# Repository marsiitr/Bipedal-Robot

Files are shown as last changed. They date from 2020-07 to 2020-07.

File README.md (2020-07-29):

# Bipedal-Robot
Srishti 2020

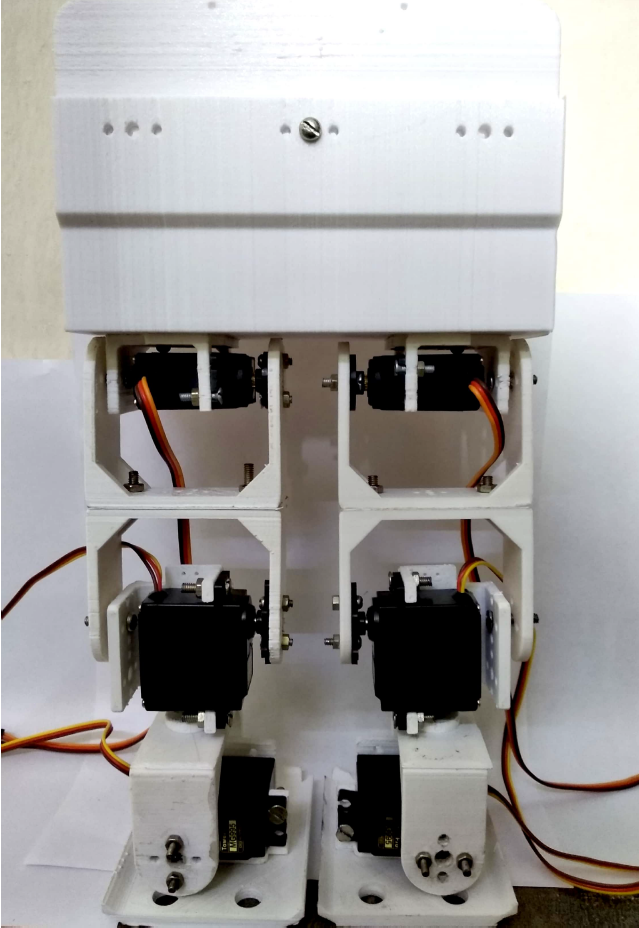
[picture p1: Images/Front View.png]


# Abstract
<div align="justify">The Bipedal Robot is a humanoid robot modeled to mimic the walking of a human, the Robot is designed to have 6 degrees of freedom in total, implying 3 degrees of freedom in each leg, 2 of which are used for moving the leg in forward or backward direction using Servo motors at each joint(hip and knee), while the other degree of freedom is used for balancing the robot using another servo motor when standing on one leg, the mechanical model is designed to avoid extra weight so that the balance of the robot is more stable. The robot is actuated by using the microcontroller Arduino.</div>

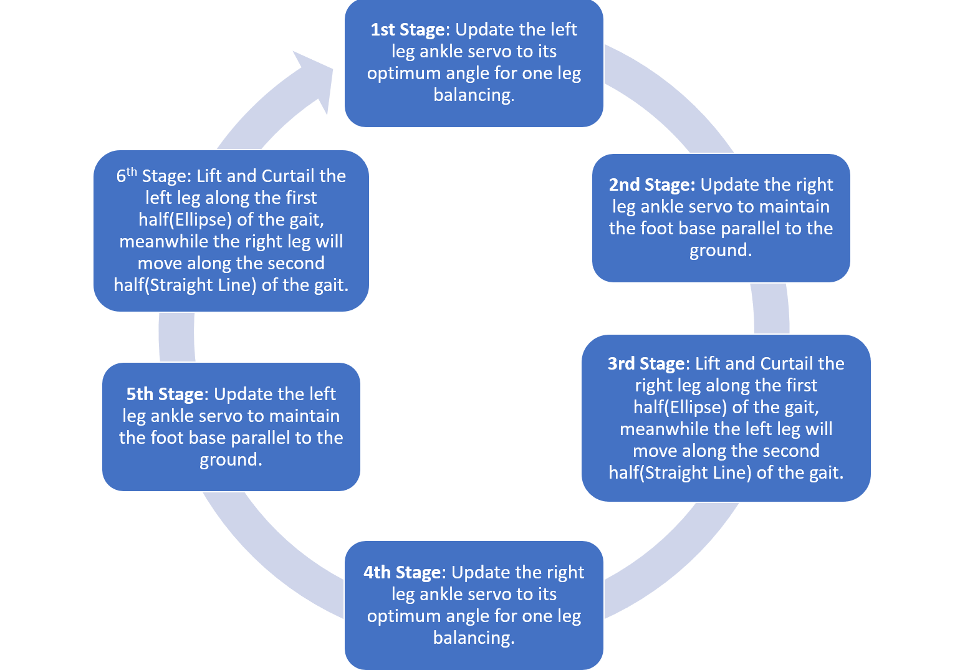
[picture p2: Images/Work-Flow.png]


## Motivation
<div align="justify">Bipedal robots are able to move in areas that are normally inaccessible to wheeled robots, such as stairs and areas littered with obstacles that make wheeled locomotion impossible, also they can be an asset which can work in hazardous conditions.</div>

## Mechanical Aspect

1. <div align="justify">Robot’s size selection - 
   Robot size plays a major role. Based on the cost of project, materials required for fabrication and the no. of actuators can be determined. In this project the size of the robot is preferred so a height of 300mm is decided which includes mountings of the control circuits, but the actual size of the robot is 230mm without controlling circuits.</div>

2. <div align="justify">Degrees of Freedom (D.O.F) - 
   Human leg has got 6 degrees of freedom (Hip – 3 D.O.F , Knee – 1 D.O.F , Ankle – 2 D.O.F) , but implementing all the 6 D.O.F is difficult due to increase in cost of project and controlling of the actuators which become complex, so in this project reduced degrees of freedom is aimed so 3 D.O.F(Ankle , Knee and Hip) per leg has been finalized.</div> 
   																								
3. <div align="justify">Foot Pad Design - 
   The stability of the robot is determined by the foot pad. Generally, there is concept that oversized and heavy foot pad will have more stability due to more contact area. But there is a disadvantage in using the oversized and heavy foot pad, because the torque requirement of the motor is more and lifting the leg against the gravity becomes difficult. By considering this disadvantage an optimal sized foot pad was used. Dimensions of the foot pad are 75x70mm.</div>
   																																		
## Electronic Aspect

1. <div align="justify">Power Source - 
   11.1 Volts 2200mAh Li-Po battery is used as the power source for powering the Arduino as well as the Servo motors, for the Servo motors IC814 chips are used to convert the battery voltage to the rating value of the Servo motors as well as ensuring optimum current flow in all the motors.</div>
   																			
2. <div align="justify">Actuation - 
   All the movement is actuated using Metal gear Servo motors, one motor is used for a single degree of freedom, so six Servo motors in all are needed for the 6 degree of freedoms in the robot.</div>
   																																	
3. <div align="justify">Motor Selection - 
   The choice of motors was based on the idea of reducing weight as well as creating a less complex feedback mechanism, hence the choice of using high torque metal gear position control DC Servo motors was appropriate under the given constraints.</div>
   																																	
4. <div align="justify">Microcontroller - 
   Arduino UNO R3 is used as the microcontroller which can operate six Servo motors at a time, enabling various types of motion such as forward, backward etc.</div>

## Cost Structure 

| Materials  | Cost(INR) |
| --- | --- |
| 6 DC Servo Motors | 3000 |
| Arduino UNO R3  |400 |
|  11.1 Li-Po Battery  | 1800 |
| Miscellaneous | 300 |
| Total | 5500 |

## Applications
1. <div align="justify">The movement of the robot can be controlled by using a remote controller.</div>
2. <div align="justify">The bipedal robot can assist humans to carry out the tasks or activities in hazardous environment which could eliminate human's risk of injury or life casualty.</div>
3. <div align="justify">They can be used for household work for the disabled or someone  suffering from any disease.</div>
4. <div align="justify">They are used at rough terrains where wheeled robots cannot be used.</div>

## Limitations
1. <div align="justify">Currently the robot has only 6 degree of freedom, so the motion has some constraints.</div>
2. <div align="justify">The bot is battery operated with small power supply, so regular change of battery is required.</div>
3. <div align="justify">Computer Vision or Ultrasonic sensing is not enabled, which means object detection cannot happen.</div>

## Future Improvements
1. <div align="justify">Size can be changed so as to human activities and task.</div>
2. <div align="justify">Degree of freedom can be increased to give proper flexibility in all directions and orientation.</div>
3. <div align="justify">Using Computer Vision for Obstacle detection, human recognition and corresponding Path planning.</div>
4. <div align="justify">Using IoT, this bot can be controlled from anywhere and can be live-streamed using webcam, it can be made autonomous using ML.</div>

## Team Members
1. [Aayush Ranjan]( https://github.com/Aayush-765 )
2. [Chirag Baghla]( https://github.com/chiragbaghla )
3. [Ila Dwiwedi]( https://github.com/ildwi)
4. [Meenakshi Gausingha]( https://github.com/Meenakshi1791)
5. [Prawal Pratap Singh]( https://github.com/ppsr7355 )
6. [Roshan Kumar Choudhary]( https://github.com/roshan-121)
7. [Upasana]( https://github.com/Upasana202)

## Mentors
1. <div align="justify">Dhruv Sehgal</div>
2. <div align="justify">Kunal Kumar</div>

## References
1. <div align="justify">https://core.ac.uk/download/pdf/29403117.pdf</div>
2. <div align="justify">https://www.researchgate.net/publication/326668524_Implementation_of_6-DOF_Biped_Footstep_Planning_Under_Different_Terrain_Conditions</div>
3. <div align="justify">https://www.youtube.com/channel/UCtwaWPOXEBysZLh1rrPzwF</div>
4. <div align="justify">https://youtu.be/2kSWHbWnVyo</div>
5. <div align="justify">https://www.solidworks.com/</div>
6. <div align="justify">https://www.arduino.cc/</div>

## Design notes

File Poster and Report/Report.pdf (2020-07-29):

## Srishti 2020

## Models and Robotics Section

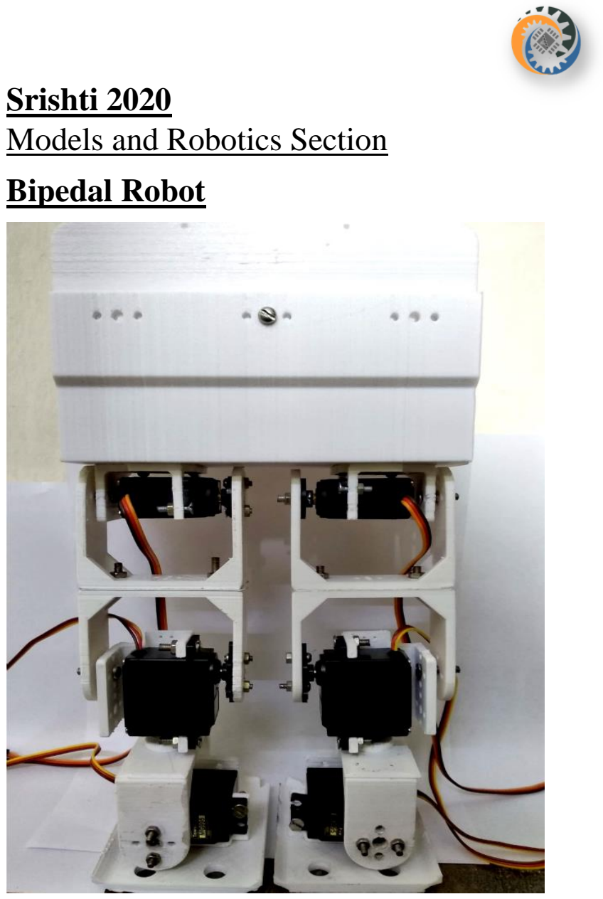
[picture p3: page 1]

## Bipedal Robot

## Abstract

The Bipedal Robot is a humanoid robot modelled to mimic the walking of a human, the Robot is designed to have 6 degrees of freedom in total, implying 3 Degrees of Freedom in each leg, 2 of which are used for moving the leg in forward or backward direction using Servo motors at each joint(hip and knee), while the other degree of freedom is used for balancing the robot using another servo motor when standing on one leg, the mechanical model is designed to avoid extra weight so that the balance of the robot is more stable. The robot is actuated by using the microcontroller Arduino and using Li-Po rechargeable batteries of 11.1 Volts as the power source.

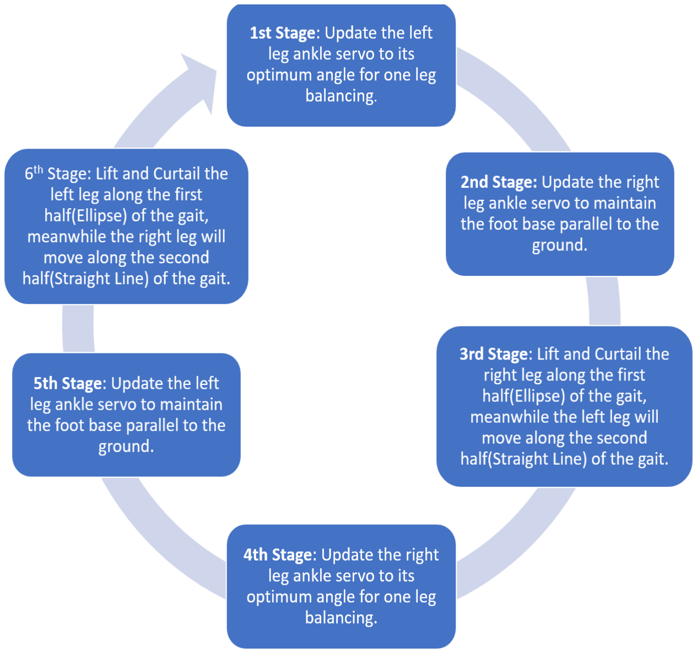
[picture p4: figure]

## Motivation

Bipedal robots are able to move in areas that are normally inaccessible to wheeled robots, such as stairs and areas littered with obstacles that make wheeled locomotion impossible, also they can be an asset which can work in hazardous conditions.

## Mechanical Aspect

Robot’s size selection

Robot size plays a major role. Based on the cost of project, materials required for fabrication and the no. of actuators can be determined. In this project the size of the robot is preferred so a height of 300mm is decided which includes mountings of the control circuits, but the actual size of the robot is 230mm without controlling circuits.

Degrees of Freedom (D.O.F)

Human leg has got 6 degrees of freedom (Hip – 3 D.O.F , Knee – 1 D.O.F , Ankle – 2 D.O.F) , but implementing all the 6 D.O.F is difficult due to increase in cost of project and controlling of the actuators which become complex, so in this project reduced degrees of freedom is aimed so 3 D.O.F(Ankle , Knee and Hip) per leg has been finalized.

Link Design

In this project we have used U-shaped, L-shaped and multipurpose Servomotor brackets like arrangement made by 3D printers and material that used is PLA for joints formation, and reducing as much extra weight as possible.

Stability of the Robot

In order to achieve effective balance, actuator will be made rotate in sequence and the robot structure will try to balance. If the balancing is not proper, in order to maintain the Centre of Mass, dead weight would be placed in invented pendulum configuration with 1 D.O.F. This Dead weight will be shifted from one side to the other according to the balance requirement.

Foot Pad Design

The stability of the robot is determined by the foot pad. Generally, there is concept that oversized and heavy foot pad will have more stability due to more contact area. But there is a disadvantage in using the oversized and heavy foot pad, because the torque requirement of the motor is more and lifting the leg against the gravity becomes difficult. By considering this disadvantage an optimal sized foot pad was used. Dimensions of the foot pad are 75*70mm.

## Electronic aspect

Power Source

11.1 Volts 2200mAh Li-Po battery is used as the power source for powering the Arduino as well as the Servo motors, for the Servo motors IC814 chips are used to convert the battery voltage to the rating value of the Servo motors as well as ensuring optimum current flow in all the motors.

Actuation

All the movement is actuated using Metal gear Servo motors, one motor is used for a single degree of freedom. The gait cycle of the robot is a combination of an ellipse as well as a straight line, when one half of the gait cycle is being executed of a certain leg then the other half of the gait cycle will be getting executed of the other leg.

Motor Selection

The choice of motors was based on the idea of reducing weight as well as creating a less complex feedback mechanism, hence the choice of using high torque metal gear position control DC Servo motors was appropriate under the given constraints.

Microcontroller

Arduino UNO R3 is used as the microcontroller which can operate six Servo motors at a time, enabling various types of motion such as forward, backward etc.

## Cost Structure

Materials | Cost (INR)
6 DC Servo Motors | 3000
Arduino UNO R3 | 400
11.1 Li-Po Battery | 1800
Miscellaneous | 300
Total | 5500

## Applications

1. The movement of the robot can be controlled by using a remote controller.
2. The bipedal robot can assist humans to carry out the tasks or activities in hazardous environment which could eliminate human's risk of injury or life casualty.
3. They can be used for household work for the disabled or someone suffering from any disease.
4. Prosthetics Walking machines can be used as walking aids for paraplegics or limb amputees. (Acosta-Marquez ´ and Bradley, 2000).
5. Agricultural work, a walking robot does less damage to the ground than a wheeled robot, and is also able to step over obstacles and move in complicated, non-smooth terrain.

## Limitations

1. Currently the robot has only 6 degree of freedom, so the motion has some constraints.
2. The bot is battery operated with small power supply, so regular change of battery is required.
3. Computer Vision or Ultrasonic sensing is not enabled, which means object detection cannot happen.

## Future Improvements

1. Size can be changed so as to human activities and task.
2. Degree of freedom can be increased to give proper flexibility in all directions and orientation.
3. Using Computer Vision for Obstacle detection, human recognition and corresponding Path planning.
4. Using IoT, this bot can be controlled from anywhere and can be live-streamed using webcam. It can be made autonomous using Machine Learning.

## Team Members

1. Aayush Ranjan ( https://github.com/Aayush-765 )
2. Chirag Baghla ( https://github.com/chiragbaghla )
3. Ila Dwiwedi ( https://github.com/ildwi)
4. Meenakshi Gausingha ( https://github.com/Meenakshi1791)
5. Prawal Pratap Singh ( https://github.com/ppsr7355 )
6. Roshan Kumar Choudhary (https://github.com/roshan-121)
7. Upasana (https://github.com/Upasana202)

## Mentors

1. Dhruv Sehgal
2. Kunal Kumar

## References

1. https://core.ac.uk/download/pdf/29403117.pdf
2. https://www.researchgate.net/publication/326668524_Implementation_of_6-DOF_Biped_Footstep_Planning_Under_Different_Terrain_Conditions
3. https://www.youtube.com/channel/UCtwaWPOXEBysZLh1rrPzwF
4. https://youtu.be/2kSWHbWnVyo
5. https://www.solidworks.com/
6. https://www.arduino.cc/

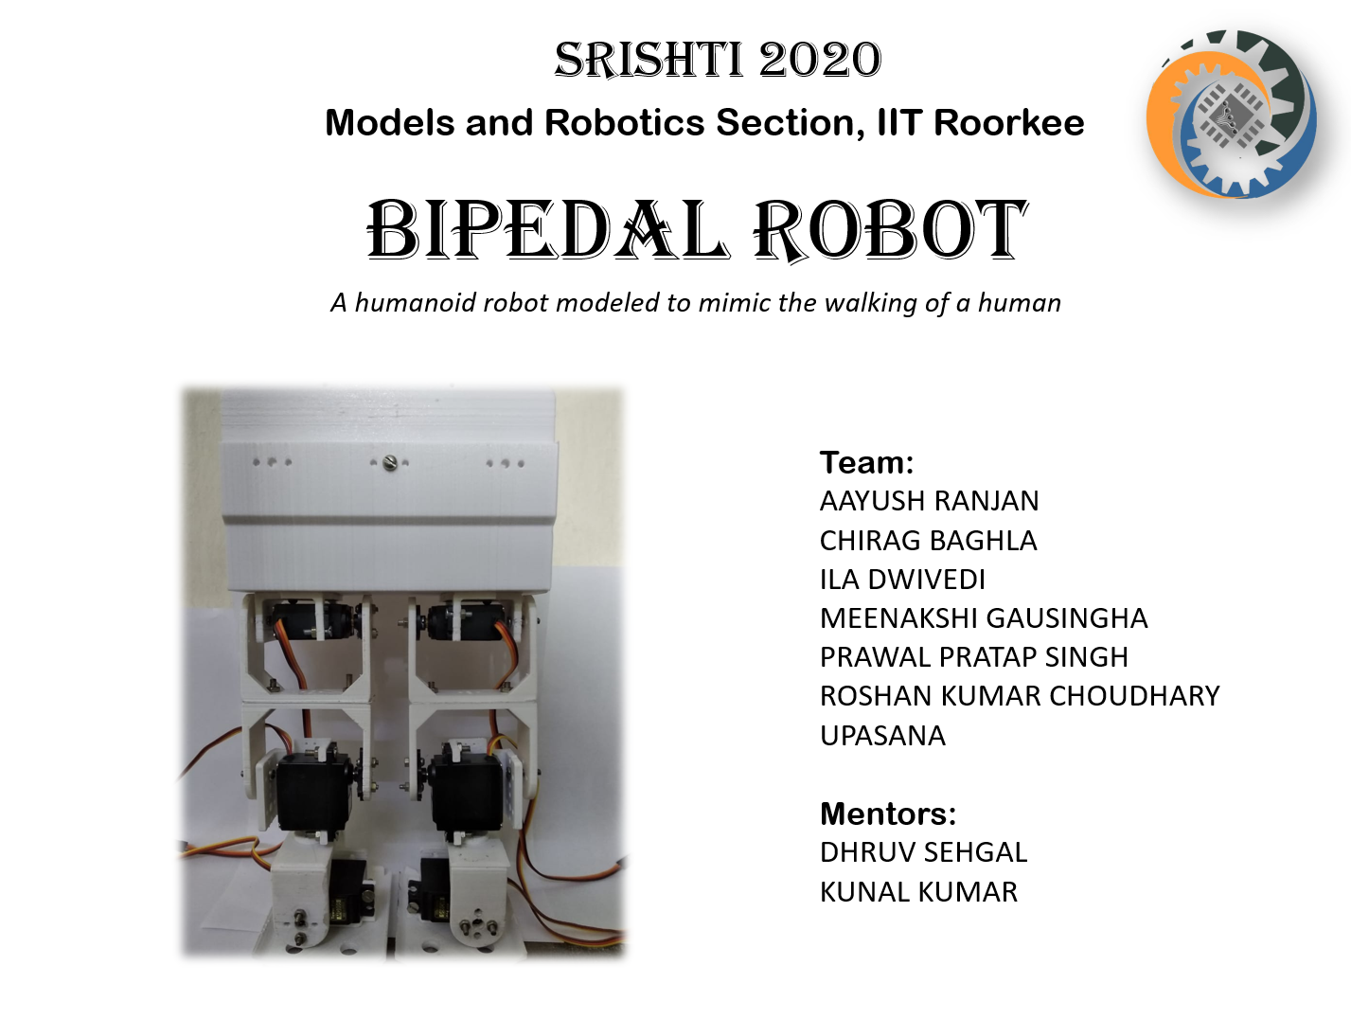
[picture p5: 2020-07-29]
Poster and Report/Poster.png

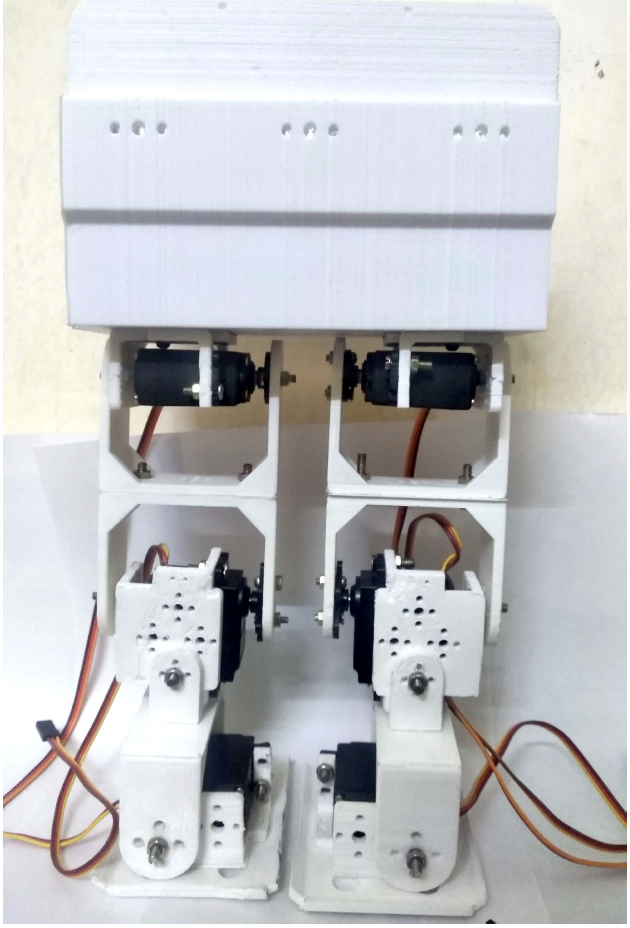
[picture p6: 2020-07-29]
Images/Back View.png

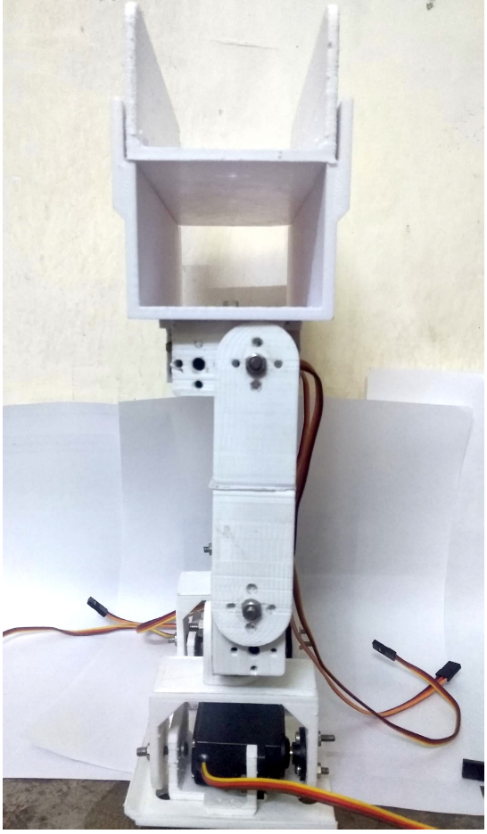
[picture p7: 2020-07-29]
Images/Side View.png

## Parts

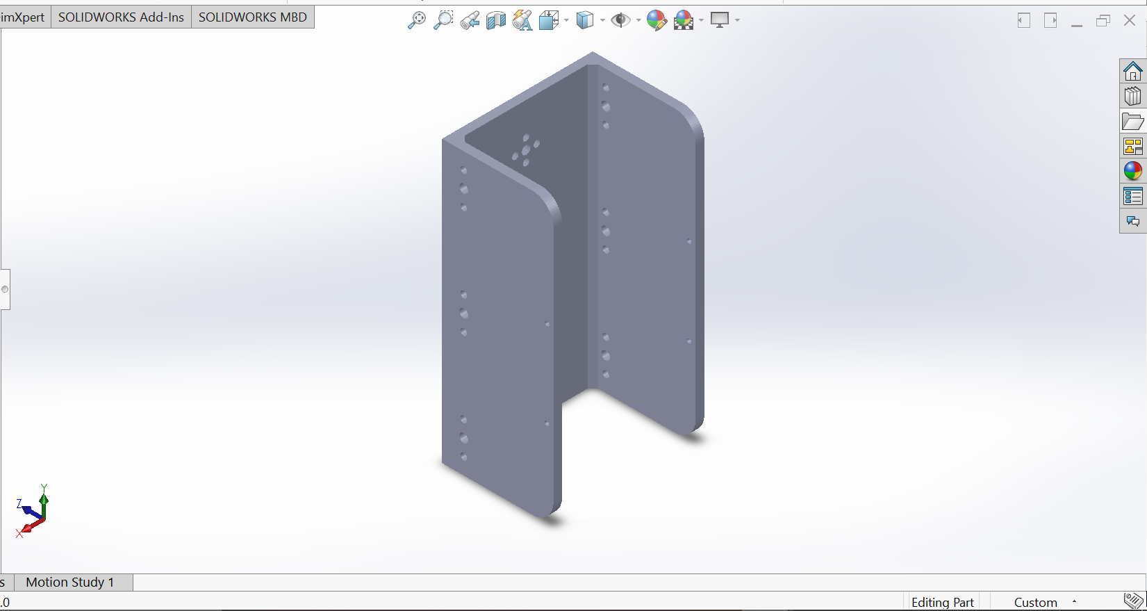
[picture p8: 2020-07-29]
Mechanical Design/Individual Parts Image files/Torso 2nd-Storey.png

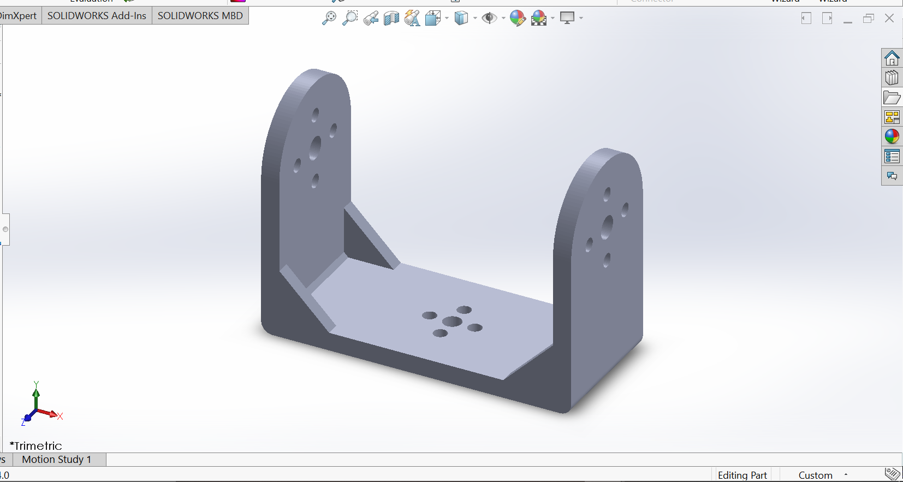
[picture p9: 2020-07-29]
Mechanical Design/Individual Parts Image files/Thigh and below Knee Link.png

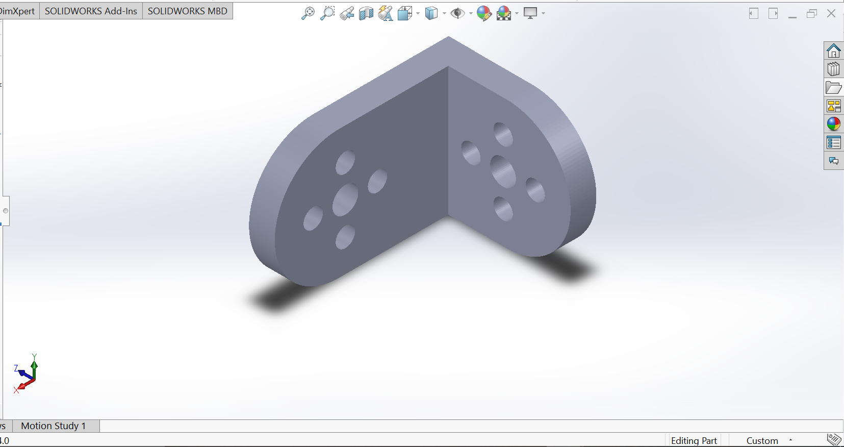
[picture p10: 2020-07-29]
Mechanical Design/Individual Parts Image files/Connector of Link and Servo Casing.png

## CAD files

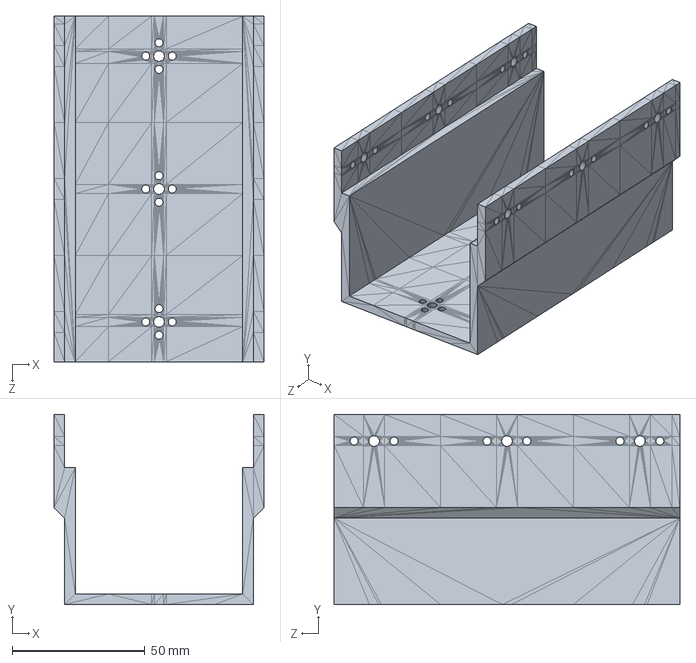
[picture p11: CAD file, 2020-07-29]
Mechanical Design/Individual Parts SOLIDWORKS files/Torso 1st-Storey.SLDPRT
79.0 x 71.5 x 130.0 mm

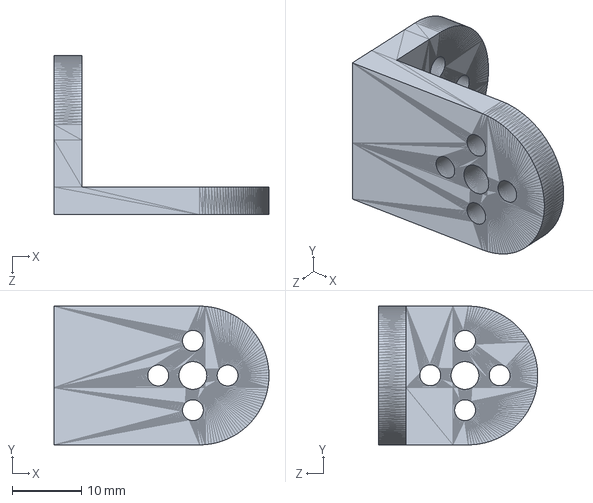
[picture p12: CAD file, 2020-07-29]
Mechanical Design/Individual Parts SOLIDWORKS files/Connector of Link and Servo Casing.SLDPRT
31.0 x 20.0 x 23.0 mm

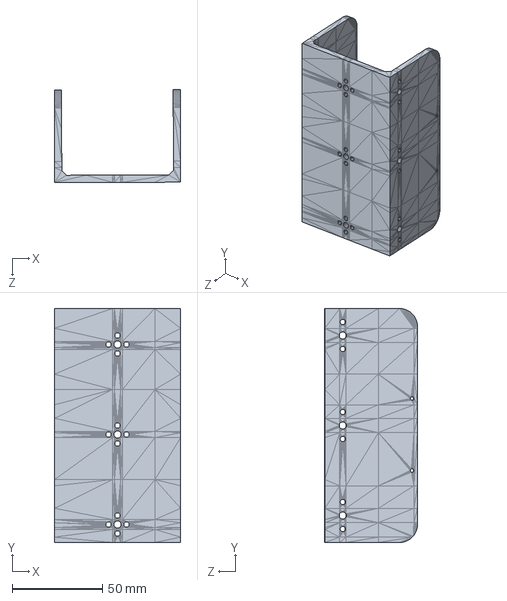
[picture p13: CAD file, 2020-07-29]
Mechanical Design/Individual Parts SOLIDWORKS files/Torso 2nd-Storey.SLDPRT
70.2 x 130.0 x 51.6 mm

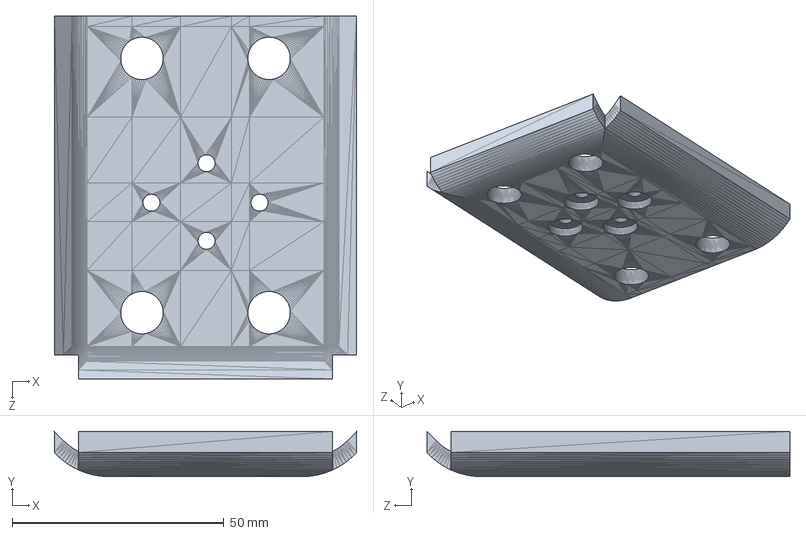
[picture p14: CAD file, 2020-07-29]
Mechanical Design/Individual Parts SOLIDWORKS files/Foot Base.SLDPRT
71.3 x 10.7 x 85.7 mm

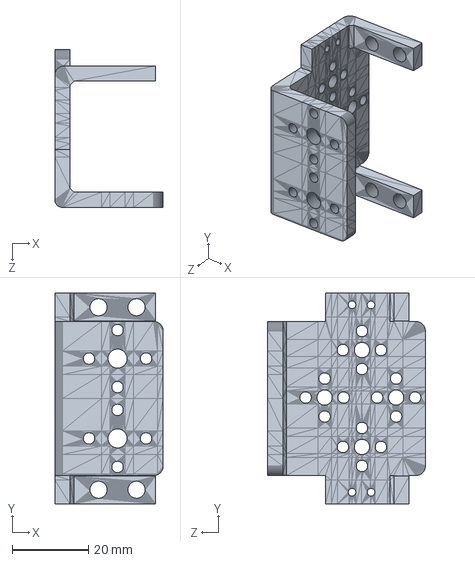
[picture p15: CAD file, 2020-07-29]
Mechanical Design/Individual Parts SOLIDWORKS files/Servo Casing.SLDPRT
28.5 x 55.5 x 41.5 mm

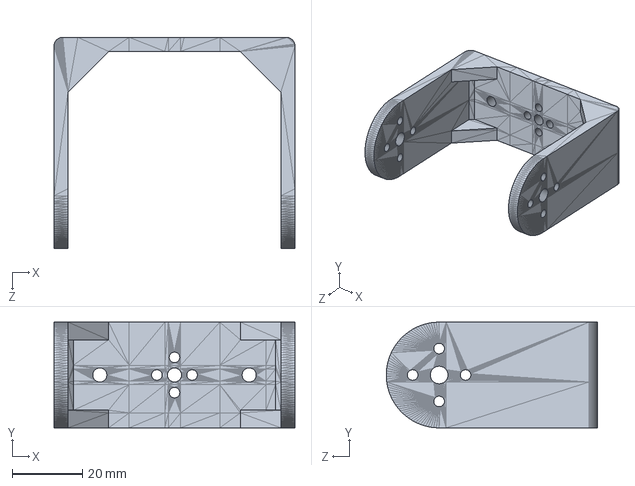
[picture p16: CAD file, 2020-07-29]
Mechanical Design/Individual Parts SOLIDWORKS files/Ankle Link.SLDPRT
68.4 x 30.0 x 60.0 mm

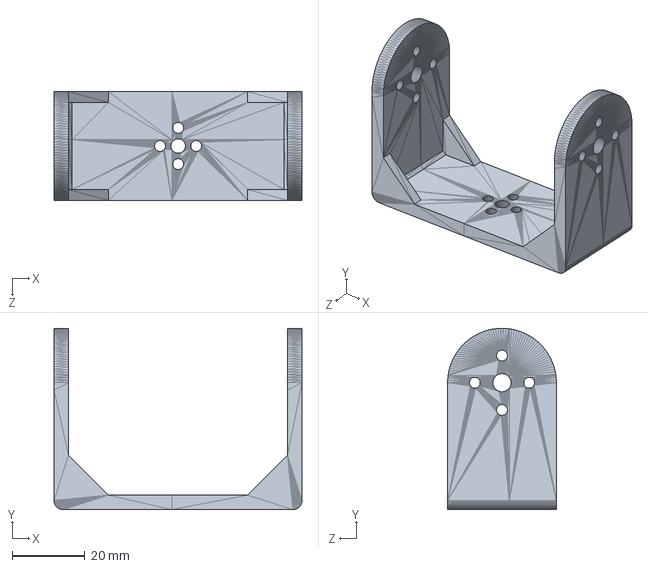
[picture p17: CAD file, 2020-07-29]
Mechanical Design/Individual Parts SOLIDWORKS files/Thigh and below Knee Link.SLDPRT
68.4 x 50.0 x 30.0 mm

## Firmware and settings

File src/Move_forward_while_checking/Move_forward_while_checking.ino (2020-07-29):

#include <Servo.h>       //include servo library

//Creating servo objects    
Servo LeftAnkleJunc;
Servo RightAnkleJunc;
Servo LeftHipJunc;
Servo RightHipJunc;
Servo LeftKneeJunc;
Servo RightKneeJunc;

//Global Variables
// Setting initial position values for each motor   
   
int LeftAnklePos = 85;  
int RightAnklePos = 98;            // for initial position, adjusting servo motors according to Bot's standing position
int LeftHipPos = 74;              
int RightHipPos = 82;
int LeftKneePos = 99;
int RightKneePos = 103;

                                   // variables for the time delay
int Delay_1 = 35;
int Delay_2 = 25;

int BalancingAngle = 12;
int ExtremeAngle = 18;

boolean FirstCycle = true;                              //Value true by default for executing first cycle
boolean a = true;                                       //Value true by default

//Functions

void StandingPosition()                                  //Standing equilibrium position for all motors
{
  LeftAnkleJunc.write(LeftAnklePos);
  RightAnkleJunc.write(RightAnklePos);                    // Updates the servo objects to the standing equilibrium positions
  LeftHipJunc.write(LeftHipPos);                          
  RightHipJunc.write(RightHipPos);                        
  LeftKneeJunc.write(LeftKneePos);                        
  RightKneeJunc.write(RightKneePos);                      
  delay(1500);
}

void Check(Servo myservo,int pos)                        //Function as to check if servo has moved to the desired angle
{
  while(a)
   {
   int state = myservo.read();
   if(state == pos)
   return;
   }
}

void Move_Forward()                                                               //forward movement function
{   
  if (FirstCycle)
  {
    for (int i = 0; i <=BalancingAngle ; i++ )                                     //angle updating for balancing at one leg
    { LeftAnkleJunc.write(LeftAnklePos-i);                                         //we can update either left foot or right foot first, left leg is used here 
      Check(LeftAnkleJunc,LeftAnklePos-i);
      
      delay(Delay_1);}                                                             // here we have iteration using -i which depends her on orientation of servo motor

    delay(Delay_2);

    for (int i = 0; i <=BalancingAngle ; i++ )                                     //angle for the second leg is now updated so that its foot is parallel to the surface
    { RightAnkleJunc.write(RightAnklePos-i);                                        //here again we have iteration of -i because there is a change in orientation of motor from before
      Check(RightAnkleJunc,RightAnklePos-i);
     
      delay(Delay_1);}                                                             //as well as we have to rotate in opposite direction so the effects cancel out 

    //Right Leg moves Forward

    for (int i = 0; i <=14 ; i++ )
    {
      RightHipJunc.write(RightHipPos+i);                                           //right leg is executing the first half(ellipse) of the gait cycle 
      Check(RightHipJunc,RightHipPos+i);
      
      RightKneeJunc.write(RightKneePos+5+i);                                       //increasing angle means lifting leg forward
      Check(RightKneeJunc,RightKneePos+5+i);
      
      LeftHipJunc.write(LeftHipPos+i);                                             //left leg is executing the second half(straight line) of the gait cycle 
      Check(LeftHipJunc,LeftHipPos+i);
      
      LeftKneeJunc.write(LeftKneePos+5+i);                                         //due to change in orientation when compared from the right leg 
      Check(LeftKneeJunc,LeftKneePos+5+i);                                         //we have to increase angle for moving the leg in backward direction
      
      delay(Delay_1);}

    delay(Delay_2);
  }

  else
  {
    //Left leg moves forward 
    for (int i = 0; i <= 30; i++ ) 
    {
      RightHipJunc.write(RightHipPos-13+i);                                         //right leg is executing the second half(straight line) of the gait cycle                                        
      Check(RightHipJunc,RightHipPos-13+i);
      
      RightKneeJunc.write(RightKneePos-22+i);                                       //increasing angle here means we are traversing the current gait cycle 
      Check(RightKneeJunc,RightKneePos-22+i);
                                                                                    //minor changes in angle values to provide necessary torque from surface
      LeftHipJunc.write(LeftHipPos-13+i);                                           //left leg is executing the first half(ellipse) of the gait cycle 
      Check(LeftHipJunc,LeftHipPos-13+i);
      
      LeftKneeJunc.write(LeftKneePos-22+i);                                         //due to change in orientation when compared from the right leg 
      Check(LeftKneeJunc,LeftKneePos-22+i);
      
      delay(Delay_1);}                                                              //we have to increase angle for moving the left leg in forward direction
  } 

  delay(Delay_2);

    //Balancing using ankle servos
    for (int i = 0; i <=BalancingAngle+ExtremeAngle ; i++ )                              //angle updating for balancing at one leg
    {                                                                                    //first servos are pushed to extreme angle for generation of tilting torque
      LeftAnkleJunc.write(LeftAnklePos-ExtremeAngle+i);                                  //increasing in both cases due to different orientations and different rotations                                             
      Check(LeftAnkleJunc,LeftAnklePos-ExtremeAngle+i);
      
      RightAnkleJunc.write(RightAnklePos-ExtremeAngle+i);                                //angle for the second foot follows that of the first foot
      Check(RightAnkleJunc,RightAnklePos-ExtremeAngle+i);
      
      delay(Delay_1);}                                                                   //angle for the second leg is now updated so that its foot is parallel to the surface

  delay(Delay_2);

  //Right Leg moves Forward

  for (int i = 0; i <=29 ; i++ )
  {
    LeftHipJunc.write(LeftHipPos+12-i);                                           //left leg is executing the second half(straight line) of the gait cycle 
    Check(LeftHipJunc,LeftHipPos+12-i);
    
    LeftKneeJunc.write(LeftKneePos+13-i);                                         //decreasing angle here means we are traversing the current gait cycle 
    Check(LeftKneeJunc,LeftKneePos+13-i);                                         //minor changes in angle values to provide necessary torque from surface
    
    RightHipJunc.write(RightHipPos+12-i);                                         //right leg is executing the first half(ellipse) of the gait cycle 
    Check(RightHipJunc,RightHipPos+12-i);
    
    RightKneeJunc.write(RightKneePos+13-i);                                       //due to change in orientation when compared from the right leg 
    Check(RightKneeJunc,RightKneePos+13-i);                                       //we have to decrease angle for moving the right leg in forward direction
    
    delay(Delay_1);
  }

  delay(Delay_2);

  //Balancing using ankle servos
  for (int i = 0; i <=BalancingAngle+ExtremeAngle ; i++ )                              //angle updating for balancing at one leg
  {                                                                                   //first servos are pushed to extreme angle for generation of tilting torque
    RightAnkleJunc.write(RightAnklePos+ExtremeAngle-i);                               //decreasing in both cases due to different orientations and different rotations 
    Check(RightAnkleJunc,RightAnklePos+ExtremeAngle-i);
   
    LeftAnkleJunc.write(LeftAnklePos+ExtremeAngle-i);                                 //angle for the second foot follows that of the first foot
    Check(LeftAnkleJunc,LeftAnklePos+ExtremeAngle-i);
    
    delay(Delay_1);                                                                   //angle for the second leg is now updated so that its foot is parallel to the surface
   }

  delay(Delay_2);

  FirstCycle = false;

}

// Set up(gets executed only once)

void setup()
{
  

                                                                        //setting output for motors
  LeftAnkleJunc.attach(11);                                             // attaches the servo on pin 9 to the servo object
  RightAnkleJunc.attach(10);                                            // attaches the servo on pin 4 to the servo object
  LeftHipJunc.attach(9);                                                // attaches the servo on pin 11 to the servo object
  RightHipJunc.attach(6);                                               // attaches the servo on pin 6 to the servo object
  LeftKneeJunc.attach(5);                                               // attaches the servo on pin 10 to the servo object
  RightKneeJunc.attach(3);                                              // attaches the servo on pin 5 to the servo object



  StandingPosition();                                                   //equilibrium position
  delay(3000);                                                          //delay 3 seconds
  
}


// Loop gets executed continously
void loop()
{
 Move_Forward();
 }

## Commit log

2020-07-27 Added solidworks files and images
    [Ankle Link.SLDPRT, Connector of Link and Servo Casing.SLDPRT, Foot Base.SLDPRT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]
2020-07-27 Revert "Merge branch 'master' of https://github.com/Aayush-765/Bipedal-Robot"
    This reverts commit e706407083f748ffa45984f206981fb5aab0ac26, reversing
    changes made to cdcb3773b76bb6e26ada1db7cfe3c459672bb33d.
    [Ankle Link.SLDPRT, Connector of Link and Servo Casing.SLDPRT, Foot Base.SLDPRT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]
2020-07-27 Added Solidworks files of parts
    [Ankle Link.SLDPRT, Connector of Link and Servo Casing.SLDPRT, Foot Base.SLDPRT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]
